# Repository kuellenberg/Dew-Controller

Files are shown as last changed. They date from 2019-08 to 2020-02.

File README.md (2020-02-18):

# Dew Controller

Microcontroller based project to control dew heater straps used on a telescope.

## Specification
* Operating voltage: 12V dc
* Power consumption (idle): t.b.d.
* 4 independently controlled heater channels
  * RCA jacks
  * Electronic overcurrent and short circuit protection
  * Total output current: 3.5 A max.
* 12 x 2 OLED display
* External temperature and humidity sensor connected via RS232 interface
  * Uses Silicon Labs Si7006 precision sensor
    * +/-1°C max.
    * +/-5% RH max.
* Auxiliary NTC temperature sensor input for testing and calibration
* User-friendly menu with rotary encoder input

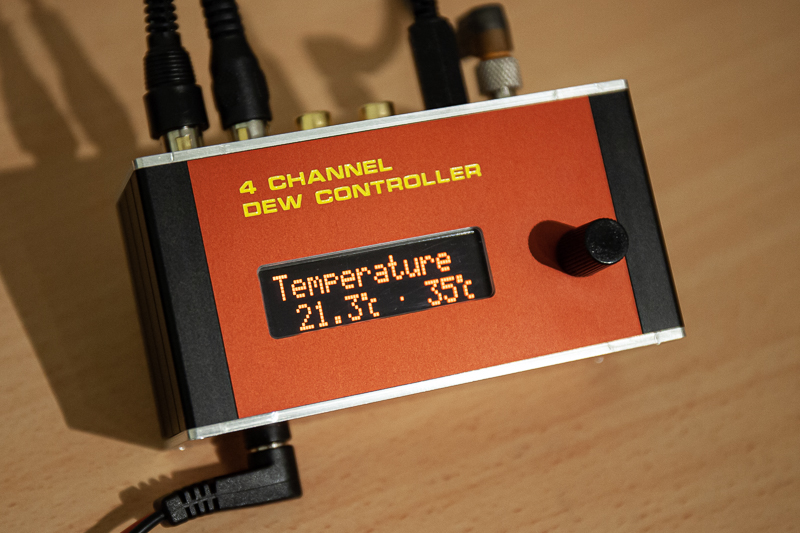
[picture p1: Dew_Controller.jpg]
Dew controller


## Theory of operation
The dew controller continuously calculates the required heating power for each connected dew heater strap based upon lens diameter and current temperature and humidity conditions. By carefully controlling the heating power negative seeing effects caused by undesired air movements are reduced to a minimum.
The underlying algorithm compensates for the rate of heat flow from the telescope lens to the cold sky, assuming that the telescope is equipped with a dew shield and only the circular area of the lens is exposed to the sky. An adjustable 'fudge factor' copes with all other deficiencies, like lack of thermal insulation from the heater straps. The theory gives very simular results to the rule of thumb given by [1].

## Hardware
### Controller Unit
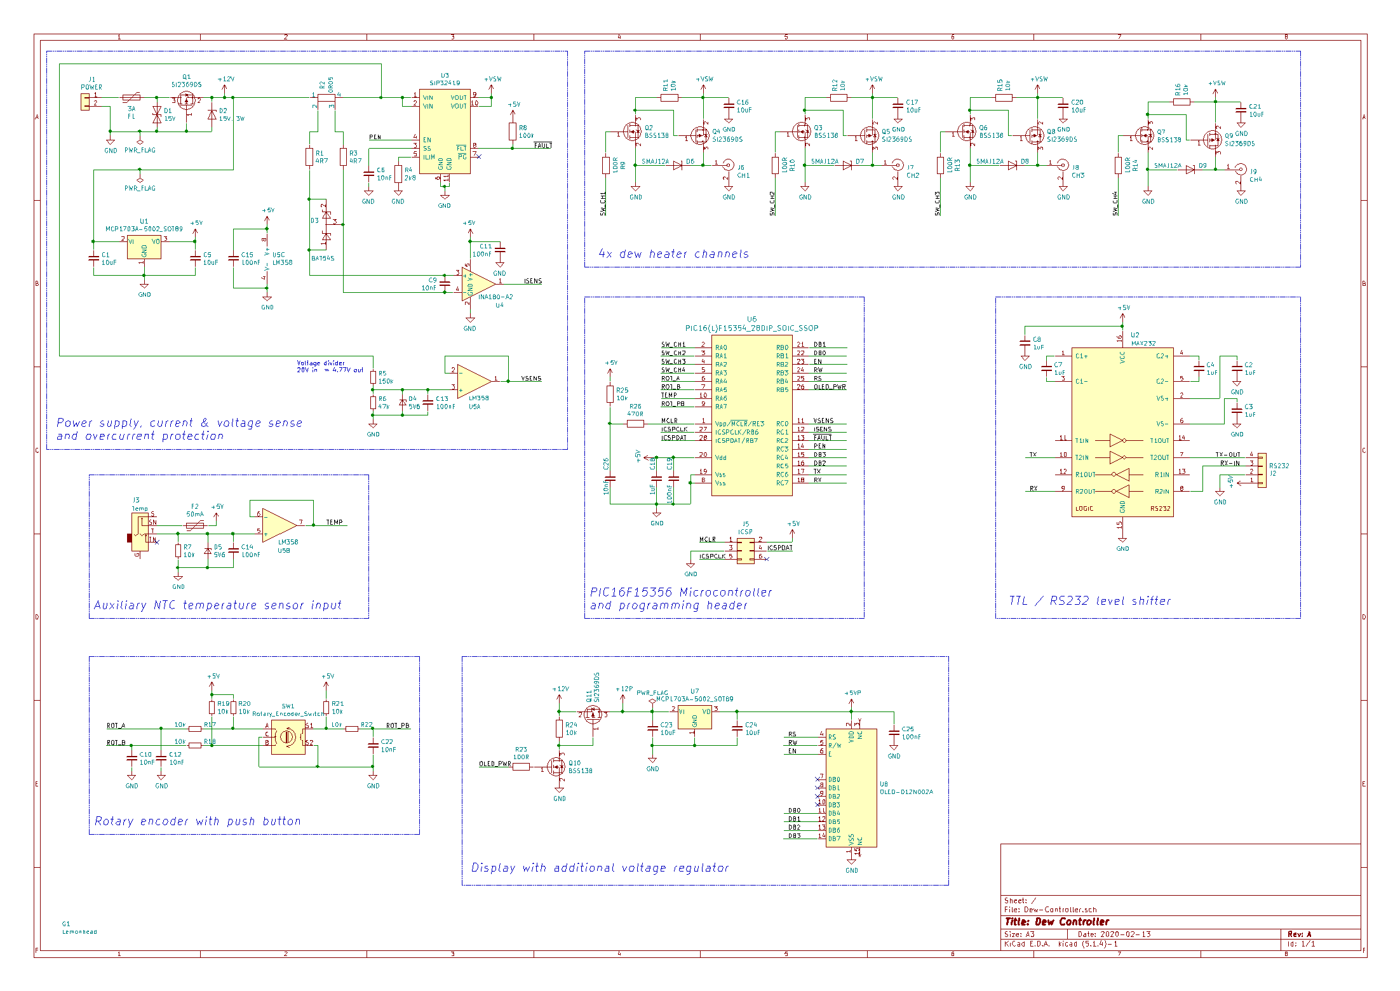
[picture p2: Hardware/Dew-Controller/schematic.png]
Schematic Dew Controller

The dew controller is build around a PIC16F15356 microcontroller with 16k words of flash memory and 2kB of RAM. It is configured to run at a clock frequency of 4.0 MHz, generated by its internal oscillator. With hindsight, regarding flash memory size and the string constants required by the menu system, the part wasn't the optimal choice. Without compiler optimizations the code doesn't fit on the device. For the next revision of the hardware a pin compatible PIC18F should be considered.

Since the controller has to be capable of measuring the current on each heater channel, the circuit comprises a TI INA180 high side current sense amplifier. To reduce cost and complexity, only a single amplifier is used and firmware measures the current of each channel sequentially. As for overcurrent and short circuit protection, an integrated solution is used. The Vishay SiP32419 is a load switch with programmable current limit up to 3.5A and eliminates the need for a conventional fuse (for which you'll never bring any spares, when you operate the device on a field trip).

The input voltage is measured with a simple voltage divider, buffered by 1/2 LM358. The other half of the Opamp is used for buffering the auxiliary NTC temperature sensor input.

It turned out that the switch mode regulator used on the OLED display module injects a lot of conducted noise back into the supply rails, which seriously impacts the performance of the microcontroller's ADC. The easiest way to block the noise from getting into the microcontroller was using a dedicated linear regulator for the display module. The regulator can be turned off via a MOSFET to save power during standby operation.

The device's menu system is entirely operated by a single rotary encoder with integrated push button. Although the quadrature signals are rudimentary low pass filtered, further debouncing is required in software.

High side P-channel MOSFETs are used to operate the four heater channels. 

The external temperature and humidity sensor is connected via an RS-232 interface, providing flexibility when testing different types of sensors. Although technically, the RS-232 level shifter isn't necessary if short cables are used, it gives good ESD protection and some extra noise immunity.

#### Case design
The housing is designed with [Schaeffer AG Frontplatten Designer](https://www.schaeffer-ag.de/frontplatten-designer)

### Sensor Box
The sensor circuit is very simple. It uses the PIC16F325 with 8k words flash memory and 1kB RAM. Unlike the controller circuit, it is powered by a 3.3V regulator. The Si7006 temperature and humidity sensor via connected I2C. RS-232 level shifting is done by a MAX3232. The PCB is designed to fit into a Hammond 1551 case with custom lid.

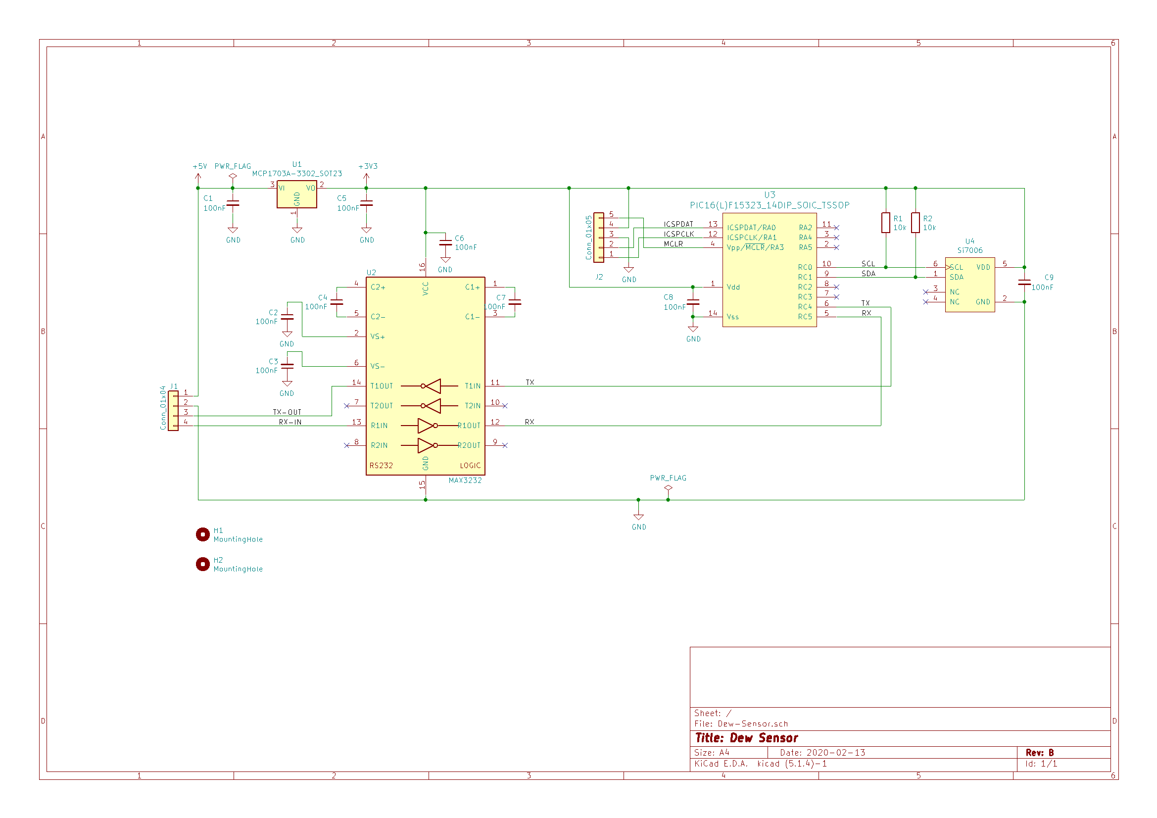
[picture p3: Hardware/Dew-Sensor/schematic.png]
Schematic Dew Sensor


## Firmware
Firmware development is done in MPLAB X with XC8 compiler. 

t.b.c.

___
[1]: G. D. Roth, Handbuch für Sternfreunde. Band 1: Technik und Theorie. ISBN 978-3-662-35367-7

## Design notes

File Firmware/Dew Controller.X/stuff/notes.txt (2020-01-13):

--- DATA STRUCTURE ---
--- GLOBAL ---
voltage
voltage min 
actual power 
temperature
humidity
dewpoint
temp_aux
dp offset
sky temp
fudge factor
groupA[4], groupB[4]

--- PER CHANNEL ---
current
max power Pmax
power required Preq
power attained Patt
duty cycle required DCreq
duty cycle attained DCatt
mode:auto|manual
status:on|off|open|short|disabled|removed
lens diameter

--- PERSISTENT DATA ---
chX
	lens dia
	mode (auto|manual)
	power

--- STATUS WORD ---
0 = ok, 1 = warning
Battery low
No sensor unit
No aux temp
typedef struct {
	unsigned BATLO:1;
	unsigned NOSENSOR:1;
	unsigned NOAUXTEMP:1;
} STATUS

--- ERROR MESSAGE ---
signed int8_t g_mp = -1;
function addMessage(message number)
	add message to message stack
	uint8_t messages[MESSAGE_STACK];
	if mp <= MESSAGE_STACK mp++;
	else f*ck it
	messages[mp] = message number;

function showMessages()
	static scrollPos;
	scroll through message[mp]
	if key mp-- & scrollPos = 0;

--- MAIN LOOP ---
read temp, humi, dp over rs232
	no data?
		if STATUS.NOSENSOR == 0 
			warning: check sensor 
		STATUS.NOSENSOR = 1;
		
read aux temp
	value out of range?
		STATUS.NOAUXTEMP = 1;
		
read voltage
read current
calc total power

current > [max load switch current] -> overcurrent (shouldn't happen)
	turn all channels off
	turn off load switch
		measure current again
		still overcurrent?
			show error!
	show error!

test voltage level
	voltage < [turn off]
		turn off load switch
		turn off oled
		power save 
	voltage min > [turn off] < [warn low]
		show warning low bat
	voltage > [warn high] < [crit]
		show warning high bat
	voltage > [crit]
		turn off oled power and load switch
		power save

calculate required power for each heater
	thermal radiation / stefan bolzman law
		epsilon = 0,95
		rho = 5,67e-8
		d = 0,0254 * lens dia
		A = PI * d^2 / 4
		T1 = tau + offset + 273,15
		T2 = tsky + 273,15
		phi = epsilon * rho * A * (T1^4 - T2^4)		
		
	Approx. heater temp. required
		p = 2 * PI * 0,0254 * lens dia
		b = 0,03 (width heat strip)
		A = p * b
		k = 0,85 (glas)
		Rth = lens dia/2 * (k * A)
		dt = phi * Rth - tau
	
	Preq = phi * fudge factor

control loop idle?
	test each heater
		if not disabled
			switch on 
			read voltage
			read current
			switch off
			store min. voltage
			current < xxx -> open
				if status changed?
					status = removed
					show warning heater removed
			current > xxx -> short
				fault detected? 
					status = disabled
					clear fault (cycle load switch)
					show warning heater short
			calculate Pmax
				Pmax = voltage * current
		
	calculate duty cycle for each channel
		DC = Pmax / Prequired
	
	optimize channel utilization
	start control loop
	
show warnings

show menu
	
--- INTERRUPT SERVICE ROUTINES ---
control loop (every 100ms)
	if not idle?
		counter < 1000?
			counter++;
		foreach channel in groupA
			counter <= DC?
				switch on
			else
				switch off
				channel in groupB?
					counter <= DC?
						switch on
					else 
						switch off
		idle = true

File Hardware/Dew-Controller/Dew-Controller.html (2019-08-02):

# BOM Rev

Date

Company

Comment 1

Comment 2

Comment 3

Comment 4

Total Parts

# 92 (Unique 43)

Ref

Qty

Value

Footprint

Datasheet

Manufacturer

Mouser

[C] -

C1 C5 C23 C24

4

10uF

Capacitor_SMD:C_1206_3216Metric

~

GRJ31CR71E106KE11L

81-GRJ31CR71E106KE1L

C2 C3 C4 C7 C8

5

1uF

Capacitor_SMD:C_0805_2012Metric

~

CC0805KKX7R9BB105

603-CC805KKX7R9BB105

C6 C9 C10 C12 C22 C26

6

10nF

Capacitor_SMD:C_0603_1608Metric

~

C0603Y103K5RACAUTO

80-C0603Y103K5RAUTO

C11 C13 C14 C15 C19

5

100nF

Capacitor_SMD:C_0603_1608Metric

~

C0603X104K5RAC7411

80-C0603X104K5R7411

C16 C17 C20 C21

4

10uF

Capacitor_SMD:C_1206_3216Metric

~

TCJA106M025R0150

581-TCJA106M025R0150

C18

1

1uF

Capacitor_SMD:C_0603_1608Metric

~

CGA3E1X7R1E105K080AE

810-CGA3E1X7R1E105KA

C25

1

100nF

Capacitor_SMD:C_0805_2012Metric

~

885012207098

710-885012207098

[D] -

D1

1

15V

Diode_SMD:D_SMB

~

SMBJ15CA-Q

652-SMBJ15CA-Q

D2

1

15V, 3W

Diode_SMD:D_SMB

~

1SMB5929BT3G

863-1SMB5929BT3G

D3

1

BAT54S

Package_TO_SOT_SMD:SOT-23

https://www.diodes.com/assets/Datasheets/ds11005.pdf

BAT54S-7-F

621-BAT54S-F

D4 D5

2

5V6

Diode_SMD:D_SOD-523

~

MM5Z5V6T1G

863-MM5Z5V6T1G

D6 D7 D8 D9

4

SMAJ12A

Diode_SMD:D_SMA

~

SMAJ12A

576-SMAJ12A

[F] -

F1

1

3A

ak:Fuse_2920_7451Metric

~

0ZCF0300BF2C

530-0ZCF0300BF2C

F2

1

50mA

ak:Fuse_0603_1608Metric

~

MH2029-601Y

652-MH2029-601Y

[G] -

G1

1

Lemonhead

ak:lemonhead

[J] -

J1

1

POWER

Connector_JST:JST_XH_B02B-XH-A_1x02_P2.50mm_Vertical

~

J2

1

RS232

Connector_JST:JST_XH_B04B-XH-A_1x04_P2.50mm_Vertical

~

J3

1

Temp

ak:MJ-2509N

~

MJ-2509N

490-MJ-2509N

J5

1

ICSP

ak:MicroMatch-Female-6P

~

215079-6

571-215079-6

J6

1

CH1

ak:PJRAN1X1U

~

PJRAN1X1U03AUX

502-PJRAN1X1U03AUX

J7

1

CH2

ak:PJRAN1X1U

~

PJRAN1X1U03AUX

502-PJRAN1X1U03AUX

J8

1

CH3

ak:PJRAN1X1U

~

PJRAN1X1U03AUX

502-PJRAN1X1U03AUX

J9

1

CH4

ak:PJRAN1X1U

~

PJRAN1X1U03AUX

502-PJRAN1X1U03AUX

[Q] -

Q1 Q4 Q5 Q8 Q9 Q11

6

SI2369DS

Package_TO_SOT_SMD:SOT-23

~

SI2369DS-T1-GE3

78-SI2369DS-T1-GE3

Q2 Q3 Q6 Q7 Q10

5

BSS138

Package_TO_SOT_SMD:SOT-23

~

BSS138P 215

771-BSS138P215

[R] -

R1 R3

2

4R7

Resistor_SMD:R_0603_1608Metric

~

ESR03EZPJ4R7

755-ESR03EZPJ4R7

R2

1

0R05

ak:R_Shunt_Ohmite_LVK12

~

LVK12R050DER

588-LVK12R050DER

R4

1

2k8

Resistor_SMD:R_0603_1608Metric

~

AC0603FR-072K8L

603-AC0603FR-072K8L

R5

1

150k

Resistor_SMD:R_0603_1608Metric

~

RC0603FR-07150KL

603-RC0603FR-07150KL

R6

1

47k

Resistor_SMD:R_0603_1608Metric

~

SFR03EZPF4702

755-SFR03EZPF4702

R7 R17 R18 R19 R20 R21 R22 R25

8

10k

Resistor_SMD:R_0603_1608Metric

~

RC0603FR-0710KL

603-RC0603FR-0710KL

R8

1

100k

Resistor_SMD:R_0603_1608Metric

~

SFR03EZPF1003

755-SFR03EZPF1003

R9 R10 R13 R14 R23

5

100R

Resistor_SMD:R_0805_2012Metric

~

CRGP0805F100R

279-CRGP0805F100R

R11 R12 R15 R16 R24

5

10k

Resistor_SMD:R_0805_2012Metric

~

ERJ-6ENF1002V

667-ERJ-6ENF1002V

R26

1

470R

Resistor_SMD:R_0603_1608Metric

~

RC0603FR-07470RL

603-RC0603FR-07470RL

[SW] -

SW1

1

Rotary_Encoder_Switch

ak:RotaryEncoder_Alps_EC11E-Switch_Vertical_H20mm

~

EC11E183440C

688-EC11E183440C

[U] -

U1 U7

2

MCP1703A-5002_SOT89

Package_TO_SOT_SMD:SOT-89-3

http://ww1.microchip.com/downloads/en/DeviceDoc/20005122B.pdf

PIC16F15354-I/SO

579-MCP1703AT5002EMB

U2

1

MAX232

ak:SOIC-16W_5.3x10.2mm_P1.27mm

http://www.ti.com/lit/ds/symlink/max232.pdf

MAX232NSR

595-MAX232NSR

U3

1

SIP32419

ak:DFN-10-1EP_3x3mm_P0.5mm_EP1.4x2.3mm

SIP32419DN-T1-GE4

78-SIP32419DN-T1-GE4

U4

1

INA180-A2

Package_TO_SOT_SMD:SOT-23-5

http://www.ti.com/lit/ds/symlink/ina181.pdf

INA180A2IDBVR

595-INA180A2IDBVR

U5

1

LM358

Package_SO:VSSOP-8_3.0x3.0mm_P0.65mm

http://www.ti.com/lit/ds/symlink/lm2904-n.pdf

LM358LVIDGKR

595-LM358LVIDGKR

U6

1

PIC16(L)F15354_28DIP_SOIC_SSOP

Package_SO:SOIC-28W_7.5x17.9mm_P1.27mm

PIC16F15354-I/SO

579-PIC16F15354-I/SO

U8

1

OLED-012N002A

ak:OLED012N002A

http://www.newhavendisplay.com/specs/NHD-0420H1Z-FSW-GBW-33V3.pdf

O012N002ARPP5N0000

78-012N002ARPP5N0000

# BOM made with KICAD_BOM_WIZARD (https://github.com/HashDefineElectronics/KiCad_BOM_Wizard) (Generated Wed 13 Mar 2019 05:19:53 PM CET)

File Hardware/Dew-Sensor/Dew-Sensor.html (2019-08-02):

# BOM Rev

Date

Company

Comment 1

Comment 2

Comment 3

Comment 4

Total Parts

# 20 (Unique 10)

Ref

Qty

Value

Footprint

Datasheet

Manufacturer

Mouser

[C] -

C1 C2 C3 C4 C5 C6 C7 C8 C9

9

100nF

Capacitor_SMD:C_0805_2012Metric

~

885012207098

710-885012207098

[G] -

G1

1

Lemonhead

ak:lemonhead

[H] -

H1 H2

2

MountingHole_Pad

MountingHole:MountingHole_2.5mm_Pad

~

[J] -

J1

1

Conn_01x04

Connector_PinSocket_2.54mm:PinSocket_1x04_P2.54mm_Horizontal

~

TSW-104-08-L-S-RA

200-TSW10408LSRA

J2

1

Conn_01x05

Connector_PinSocket_1.27mm:PinSocket_1x05_P1.27mm_Vertical

~

M50-3030542

855-M50-3030542

[R] -

R1 R2

2

10k

Resistor_SMD:R_0805_2012Metric

~

ERJ-6ENF1002V

667-ERJ-6ENF1002V

[U] -

U1

1

MCP1703A-3302_SOT23

Package_TO_SOT_SMD:SOT-23

http://ww1.microchip.com/downloads/en/DeviceDoc/20005122B.pdf

MCP1703AT-3302E/CB

579-MCP1703AT3302ECB

U2

1

MAX3232

Package_SO:SOIC-16_3.9x9.9mm_P1.27mm

https://datasheets.maximintegrated.com/en/ds/MAX3222-MAX3241.pdf

MAX3232IDR

595-MAX3232IDR

U3

1

PIC16(L)F15323_14DIP_SOIC_TSSOP

Package_SO:SOIC-14_3.9x8.7mm_P1.27mm

PIC16F15323-I/SL

579-PIC16F15323-I/SL

U4

1

Si7006

ak:SI7006-A20

SI7006-A20-IM1R

634-SI7006-A20-IM1R

# BOM made with KICAD_BOM_WIZARD (https://github.com/HashDefineElectronics/KiCad_BOM_Wizard) (Generated Wed 20 Mar 2019 07:00:30 PM CET)

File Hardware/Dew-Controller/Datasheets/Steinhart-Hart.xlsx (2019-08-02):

R0 | 10000 |  |  | 1.97
B | 3380 |  |  | 1.68
T0 | 298.15 |  |  | 0.66
r | 0.1192855385
Rs | 33000 |  |  | 610.2996911
U | 3.3 |  |  | 9.25337405 | 0.09831235519
Iconst | 2e-05
T | R | I | U0 | U1 | U2 | ADC1 | ADC2
-30 | 129916.7384 | 2.025574555e-05 | 2.60 | 2.63 | 3.30 | 815.783723 | 1023
-20 | 75021.6899 | 3.054942024e-05 | 1.50 | 2.29 | 2.73 | 710.4794309 | 846.486244
-10 | 45168.27118 | 4.221661743e-05 | 0.90 | 1.91 | 2.09 | 591.1240036 | 646.4196146
0 | 28223.72509 | 5.390067323e-05 | 0.56 | 1.52 | 1.44 | 471.5961128 | 446.0638974
10 | 18231.39918 | 6.441362236e-05 | 0.36 | 1.17 | 0.86 | 364.0486433 | 265.7900697
20 | 12133.17001 | 7.311695588e-05 | 0.24 | 0.89 | 0.38 | 275.0135414 | 116.5471476
30 | 8294.606244 | 7.991358437e-05 | 0.17 | 0.66 | 0.00 | 205.4840319 | 0

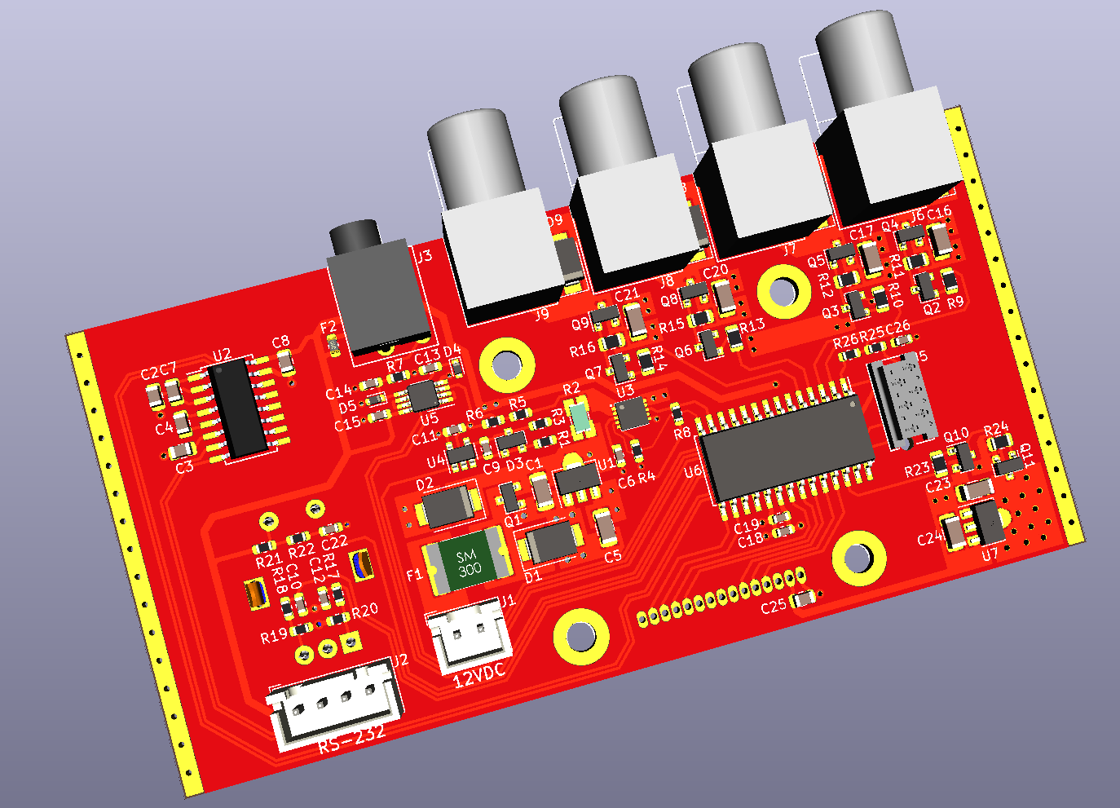
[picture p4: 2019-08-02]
Hardware/Dew-Controller/PCB.png

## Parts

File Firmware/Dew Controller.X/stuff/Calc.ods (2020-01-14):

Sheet: Tabelle1
U1 | 12
R1 | 150
R2 | 47
U2 | 2,862944162
N | 1023
Uref | 5
counts | 610
U2(counts) | 12,49662029
 | 1249280
Rsh | 0,05
A | 50
N | 1023
Uref | 5
Counts | 1
I | 0,001955034 | 195,5034213

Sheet: timer0
Fosc | 4,00E+006 | Hz
Fosc/4 | 1000000 | Hz
Presc | 128
 | 7812,5 | Hz
Postsc | 1
 | 7812,5 | Hz
Bits | 256
Tmax | 0,032768 | s
Required | 0,01 | s
TMR0 | 177,875
Actual | 0,010112 | s

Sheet: timer1
Fosc | 4,00E+006 | Hz
Fosc/4 | 1000000 | Hz
Presc | 8
 | 125000 | Hz
Bits | 65535
Tmax | 0,52428 | s
Required | 0,1 | s
TMR1 | 53035
Actual | 0,1 | s

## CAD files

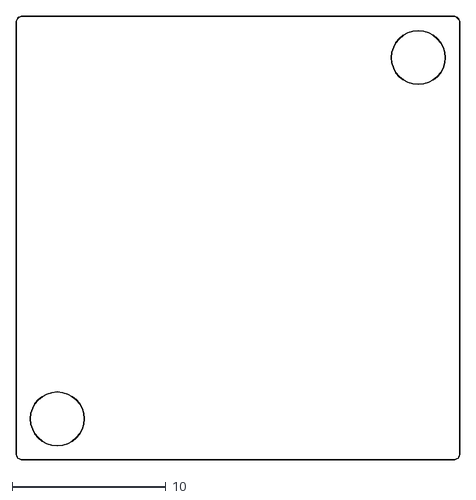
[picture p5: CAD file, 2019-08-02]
Hardware/Lid/Datasheets/outline.dxf
28.9 x 28.9

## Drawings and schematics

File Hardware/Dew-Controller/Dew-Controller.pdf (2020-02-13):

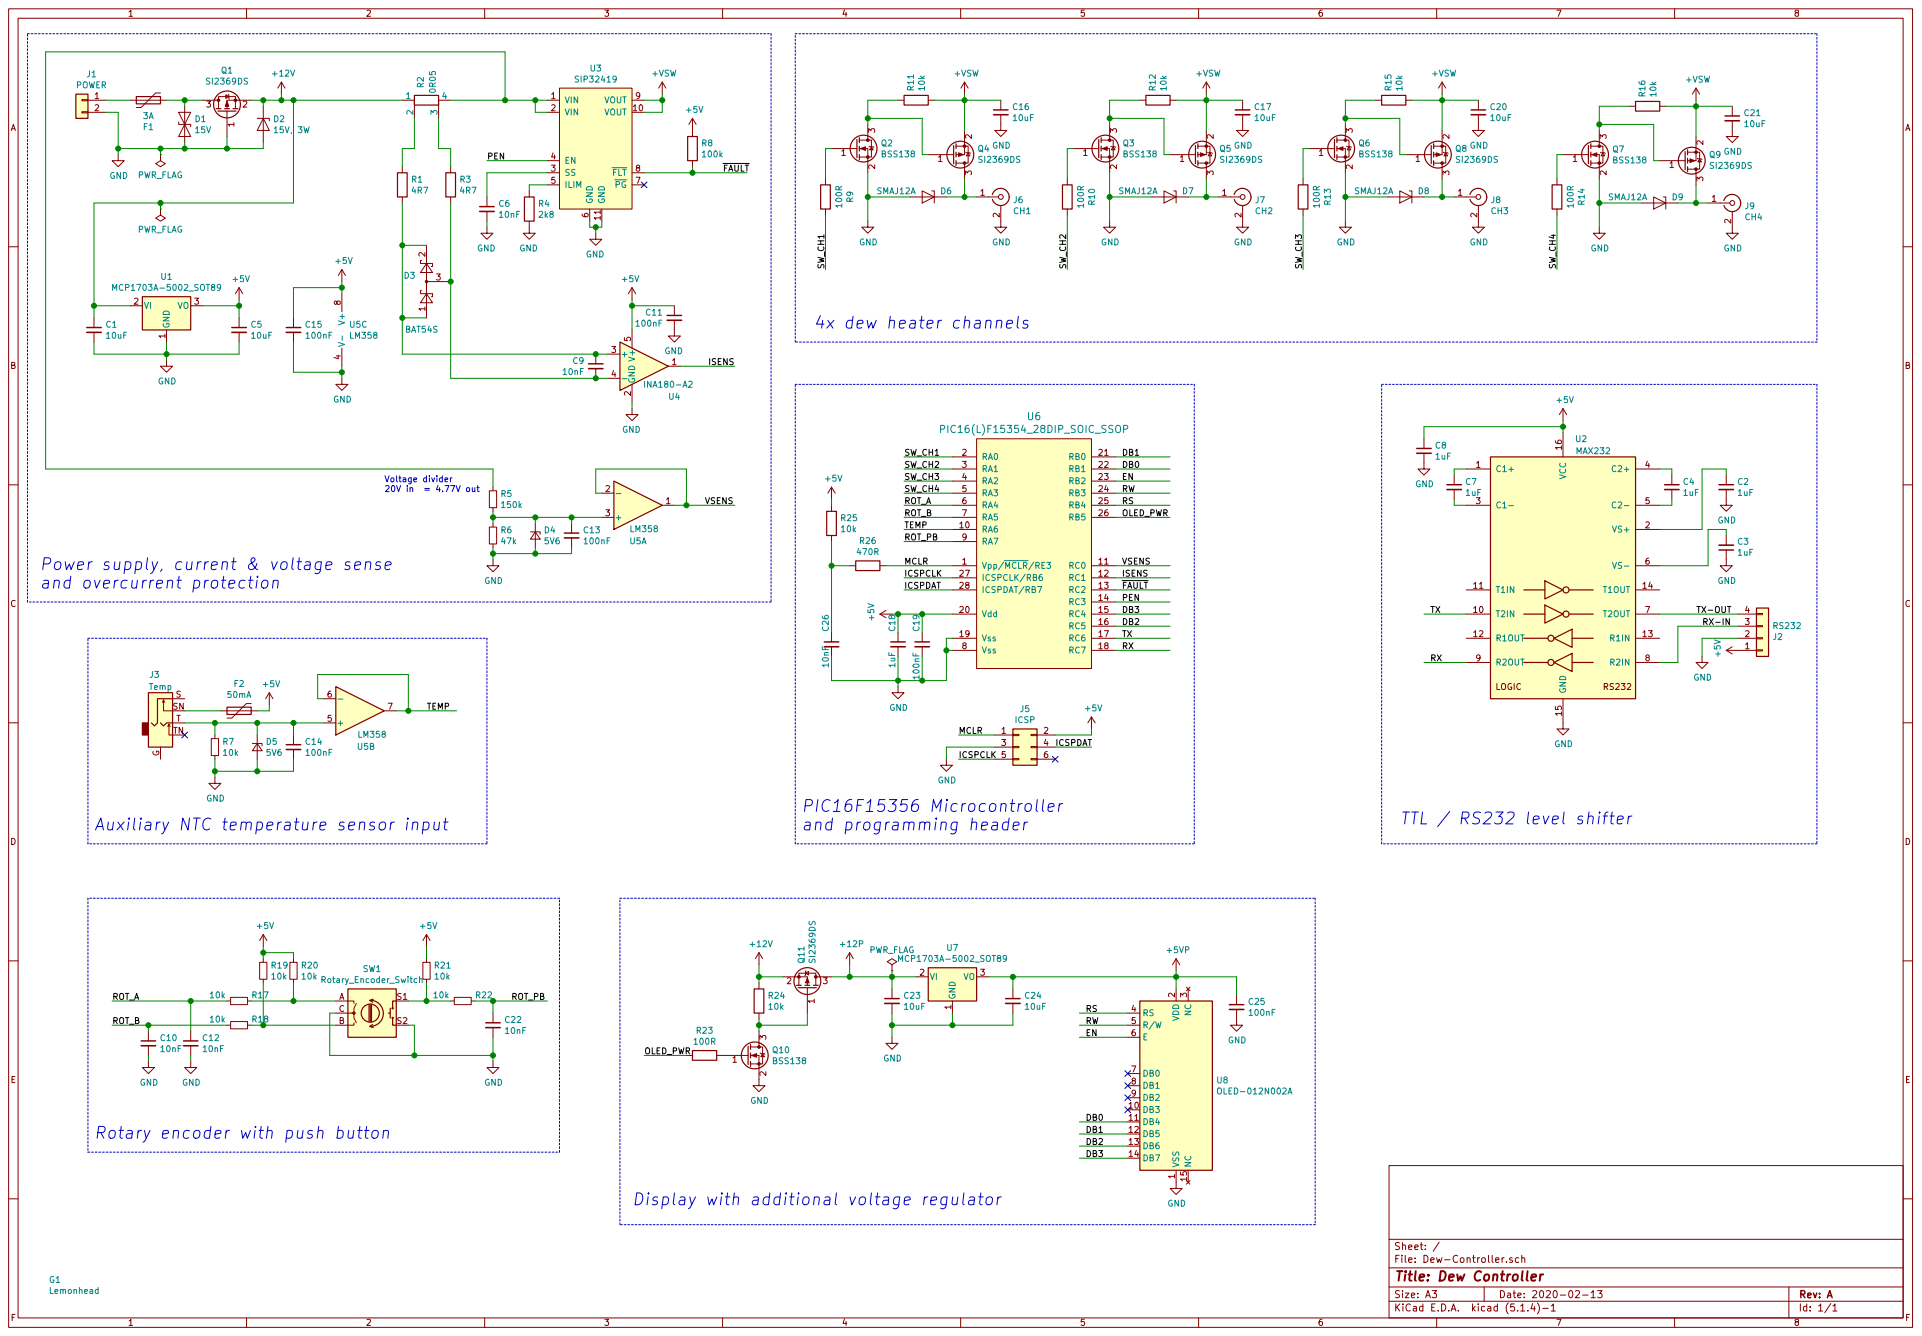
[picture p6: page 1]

Voltage divider 20V in = 4.77V out

Power supply, current & voltage sense
and overcurrent protection

RS Rotary encoder with push button

Display with additional voltage regulator

Id: 1/1 Title: Dew Controller File: Dew-Controller.sch Sheet: /

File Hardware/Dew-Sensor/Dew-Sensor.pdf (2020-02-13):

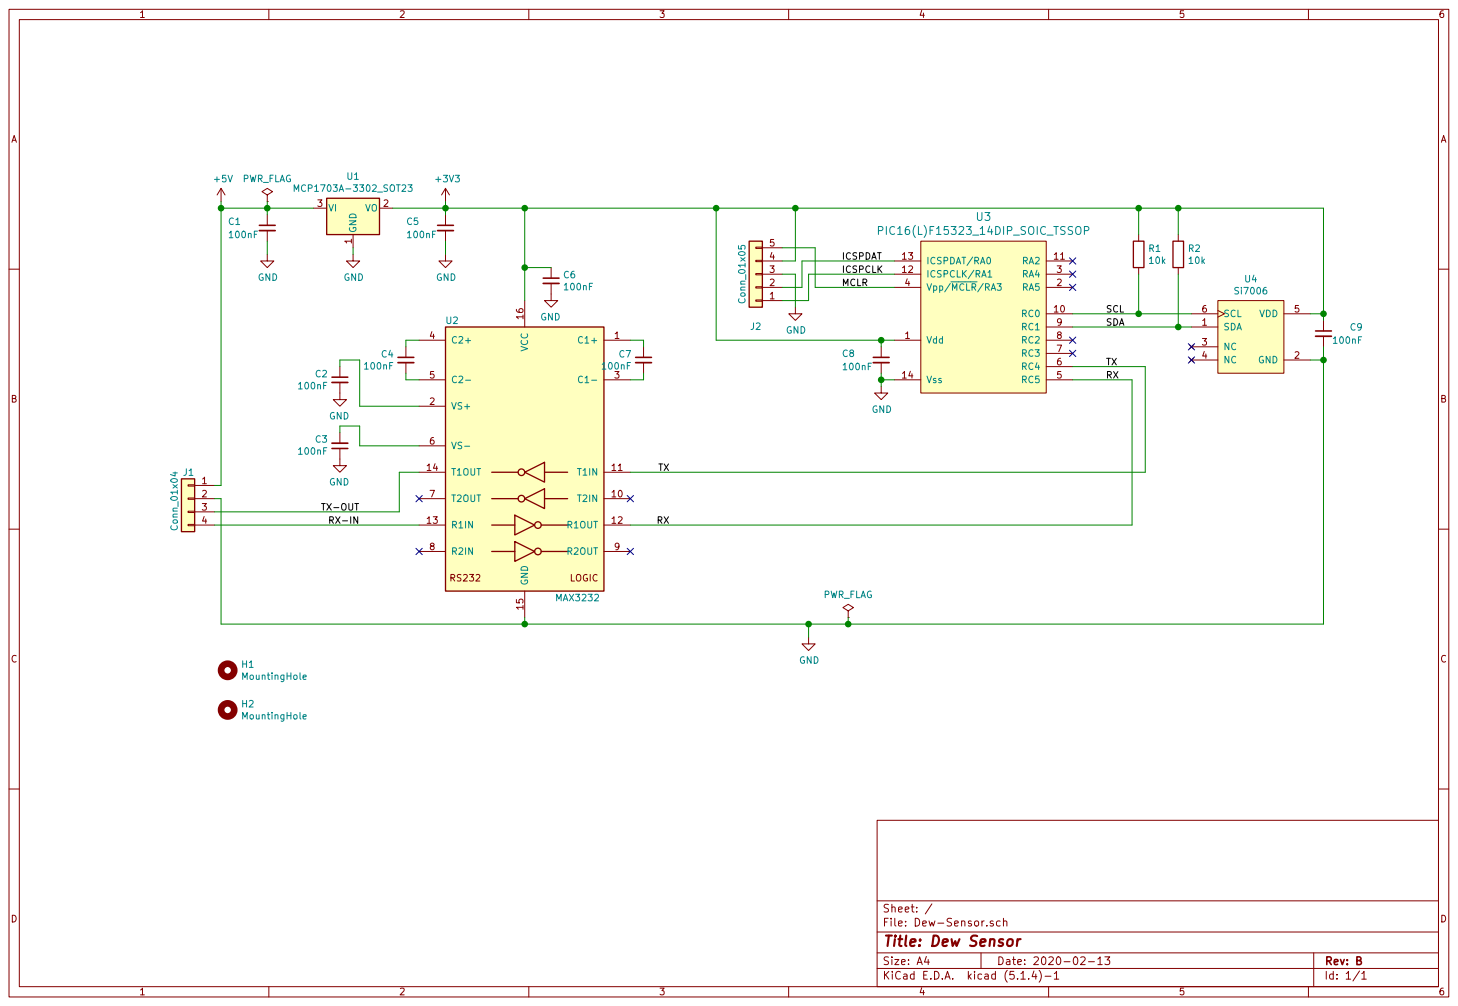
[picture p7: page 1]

3 | ICSPCLK MCLR | ICSPCLK/RA1 12

Id: 1/1 Title: Dew Sensor File: Dew-Sensor.sch Sheet: / PWR_FLAG

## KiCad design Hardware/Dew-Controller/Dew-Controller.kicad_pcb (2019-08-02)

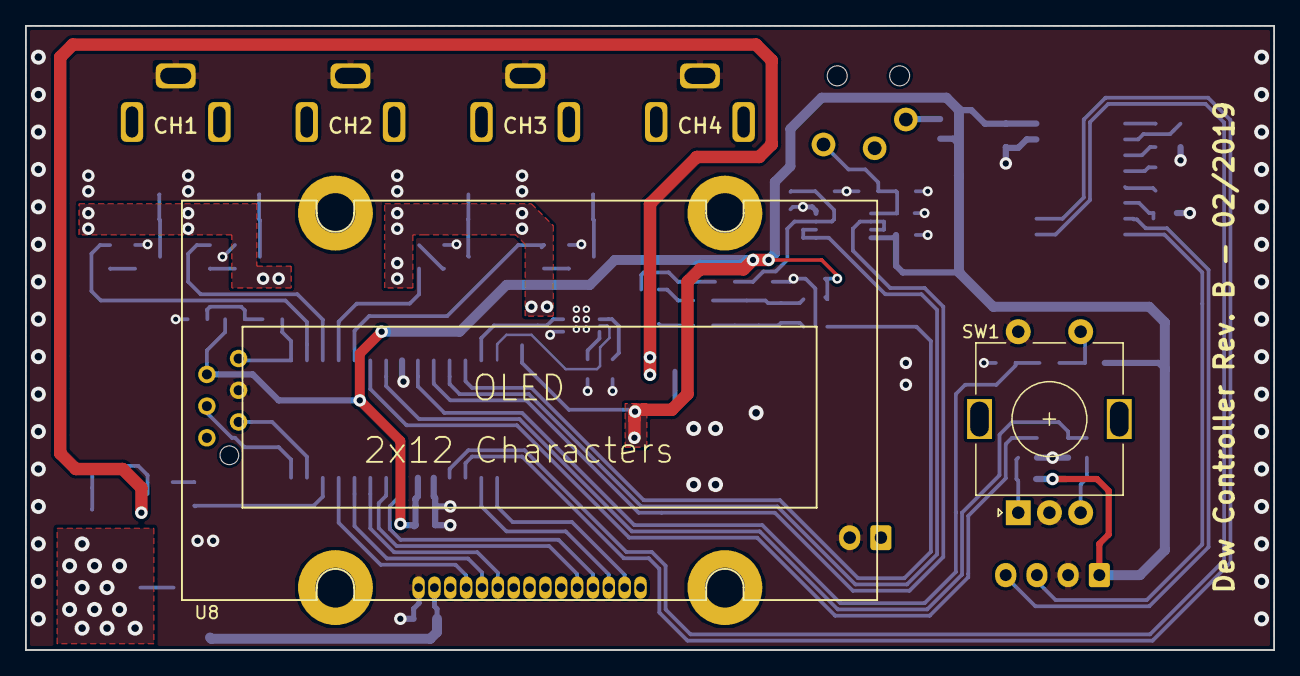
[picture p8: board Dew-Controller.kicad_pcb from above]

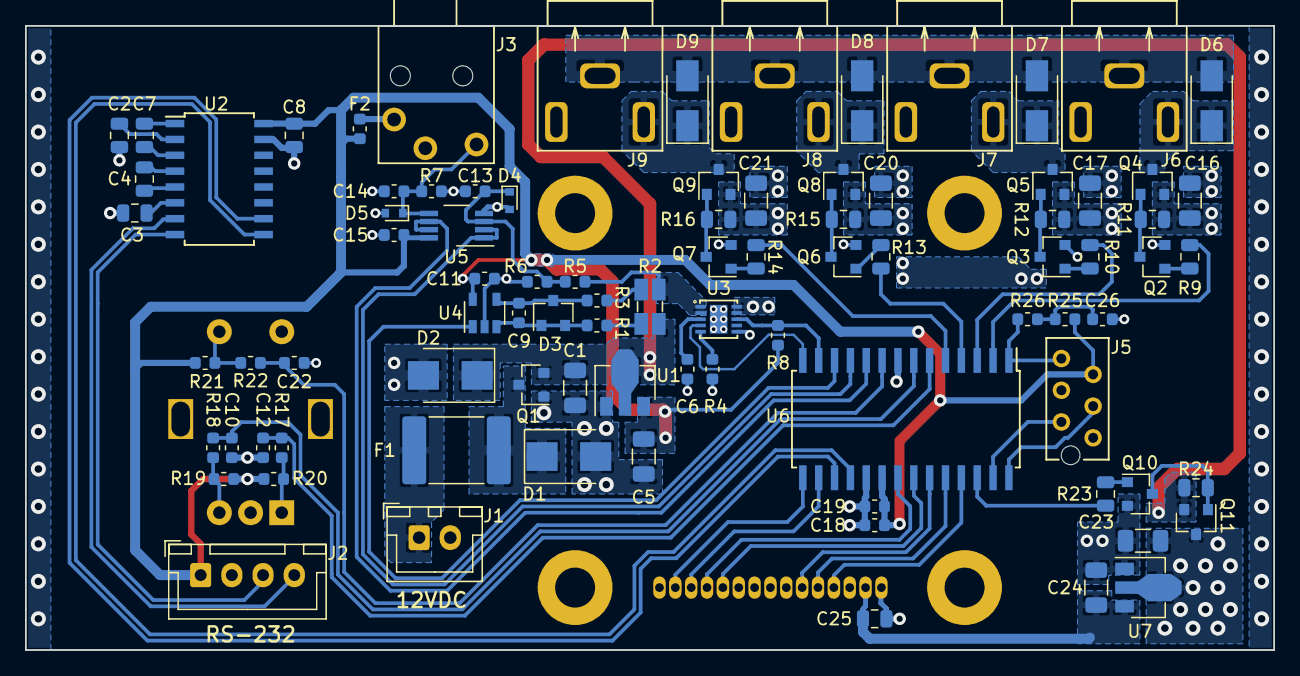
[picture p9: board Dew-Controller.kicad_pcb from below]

Board: 2 copper layers, 100.0 x 50.0 mm, 92 parts (89 on the bottom side), 69 nets.

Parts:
C1, C5, C16, C17, C20, C21, C23, C24: 10uF; C_1206_3216Metric
C2, C3, C4, C7, C8: 1uF; C_0805_2012Metric
C6, C9, C10, C12, C22, C26: 10nF; C_0603_1608Metric
C11, C13, C14, C15, C19: 100nF; C_0603_1608Metric
C18: 1uF; C_0603_1608Metric
C25: 100nF; C_0805_2012Metric
D1: 15V; D_SMB
D2: 15V, 3W; D_SMB
D3: BAT54S; SOT-23
D4, D5: 5V6; D_SOD-523
D6, D7, D8, D9: SMAJ12A; D_SMA
F1: 3A; Fuse_2920_7451Metric
F2: 50mA; Fuse_0603_1608Metric
G1: Lemonhead; lemonhead
J1: POWER; JST_XH_B02B-XH-A_1x02_P2.50mm_Vertical
J2: RS232; JST_XH_B04B-XH-A_1x04_P2.50mm_Vertical
J3: Temp; MJ-2509N
J5: ICSP; MicroMatch-Female-6P
J6: CH1; PJRAN1X1U
J7: CH2; PJRAN1X1U
J8: CH3; PJRAN1X1U
J9: CH4; PJRAN1X1U
Q1, Q4, Q5, Q8, Q9, Q11: SI2369DS; SOT-23
Q2, Q3, Q6, Q7, Q10: BSS138; SOT-23
R1, R3: 4R7; R_0603_1608Metric
R2: 0R05; R_Shunt_Ohmite_LVK12
R4: 2k8; R_0603_1608Metric
R5: 150k; R_0603_1608Metric
R6: 47k; R_0603_1608Metric
R7, R17, R18, R19, R20, R21, R22, R25: 10k; R_0603_1608Metric
R8: 100k; R_0603_1608Metric
R9, R10, R13, R14, R23: 100R; R_0805_2012Metric
R11, R12, R15, R16, R24: 10k; R_0805_2012Metric
R26: 470R; R_0603_1608Metric
SW1: Rotary_Encoder_Switch; RotaryEncoder_Alps_EC11E-Switch_Vertical_H20mm
U1, U7: MCP1703A-5002_SOT89; SOT-89-3
U2: MAX232; SOIC-16W_5.3x10.2mm_P1.27mm
U3: SIP32419; DFN-10-1EP_3x3mm_P0.5mm_EP1.4x2.3mm
U4: INA180-A2; SOT-23-5
U5: LM358; VSSOP-8_3.0x3.0mm_P0.65mm
U6: PIC16(L)F15354_28DIP_SOIC_SSOP; SOIC-28W_7.5x17.9mm_P1.27mm
U8: OLED-012N002A; OLED012N002A

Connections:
+5V: C5.1, C8.1, C11.1, C15.1, C18.1, C19.1, F2.1, J2.1, J5.2, R8.1, R19.1, R20.1, R21.1, R25.1, U1.3, U2.16, U4.5, U5.8, U6.20
+5VP: C24.1, C25.1, U7.3, U8.2
+12P: C23.1, Q11.3, U7.2
+12V: C1.1, D2.1, Q1.2, Q11.2, R2.1, R24.1, U1.2
+VSW: C16.1, C17.1, C20.1, C21.1, Q4.2, Q5.2, Q8.2, Q9.2, R11.2, R12.2, R15.2, R16.2, U3.9, U3.10
/DB0: U6.22, U8.11
/DB1: U6.21, U8.12
/DB2: U6.16, U8.13
/DB3: U6.15, U8.14
/EN: U6.23, U8.6
/ICSPCLK: J5.5, U6.27
/ICSPDAT: J5.4, U6.28
/ISENS: U4.1, U6.12
/MCLR: J5.1, R26.1, U6.1
/OLED_PWR: R23.2, U6.26
/PEN: U3.4, U6.14
/ROT_A: C12.1, R17.2, U6.6
/ROT_B: C10.1, R18.2, U6.7
/ROT_PB: C22.1, R22.1, U6.9
/RS: U6.25, U8.4
/RW: U6.24, U8.5
/RX: U2.9, U6.18
/RX-IN: J2.3, U2.8
/SW_CH1: R9.2, U6.2
/SW_CH2: R10.2, U6.3
/SW_CH3: R13.2, U6.4
/SW_CH4: R14.2, U6.5
/TEMP: U5.6, U5.7, U6.10
/TX: U2.10, U6.17
/TX-OUT: J2.4, U2.7
/VSENS: U5.1, U5.2, U6.11
/~FAULT: R8.2, U3.8, U6.13
GND: C1.2, C2.2, C3.1, C5.2, C6.2, C8.2, C10.2, C11.2, C12.2, C13.2, C14.2, C15.2, C16.2, C17.2, C18.2, C19.2, C20.2, C21.2, C22.2, C23.2, C24.2, C25.2, C26.2, D1.2, D2.2, D4.2, D5.2, D6.2, D7.2, D8.2, D9.2, J1.2, J2.2, J5.3, J6.2, J7.2, J8.2, J9.2, Q1.1, Q2.2, Q3.2, Q6.2, Q7.2, Q10.2, R4.2, R6.2, R7.2, SW1.C, SW1.S2, U1.1, U2.15, U3.6, U3.11, U4.2, U5.4, U6.8, U6.19, U7.1, U8.1
unnamed: C2.1, U2.2
unnamed: C3.2, U2.6
unnamed: C4.1, U2.4
unnamed: C4.2, U2.5
unnamed: C6.1, U3.3
unnamed: C7.1, U2.1
unnamed: C7.2, U2.3
unnamed: C9.1, D3.1, D3.2, R1.2, U4.3
unnamed: C9.2, D3.3, R3.2, U4.4
unnamed: C13.1, D4.1, R5.2, R6.1, U5.3
unnamed: C14.1, D5.1, J3.T, R7.1, U5.5
unnamed: C26.1, R25.2, R26.2
unnamed: D1.1, F1.2, Q1.3
unnamed: D6.1, J6.1, Q4.3
unnamed: D7.1, J7.1, Q5.3
unnamed: D8.1, J8.1, Q8.3
unnamed: D9.1, J9.1, Q9.3
unnamed: F1.1, J1.1
unnamed: F2.2, J3.S
unnamed: Q2.1, R9.1
unnamed: Q2.3, Q4.1, R11.1
unnamed: Q3.1, R10.1
unnamed: Q3.3, Q5.1, R12.1
unnamed: Q6.1, R13.1
unnamed: Q6.3, Q8.1, R15.1
unnamed: Q7.1, R14.1
unnamed: Q7.3, Q9.1, R16.1
unnamed: Q10.1, R23.1
unnamed: Q10.3, Q11.1, R24.2
unnamed: R1.1, R2.2
unnamed: R2.3, R3.1
unnamed: R2.4, R5.1, U3.1, U3.2
unnamed: R4.1, U3.5
unnamed: R17.1, R20.2, SW1.A
unnamed: R18.1, R19.2, SW1.B
unnamed: R21.2, R22.2, SW1.S1

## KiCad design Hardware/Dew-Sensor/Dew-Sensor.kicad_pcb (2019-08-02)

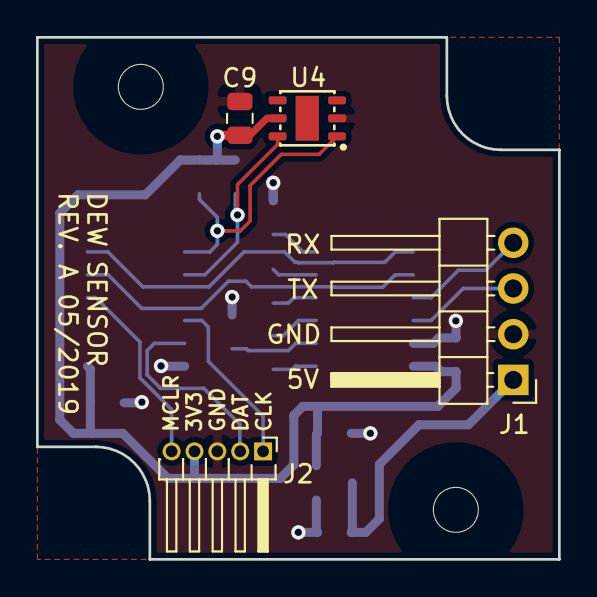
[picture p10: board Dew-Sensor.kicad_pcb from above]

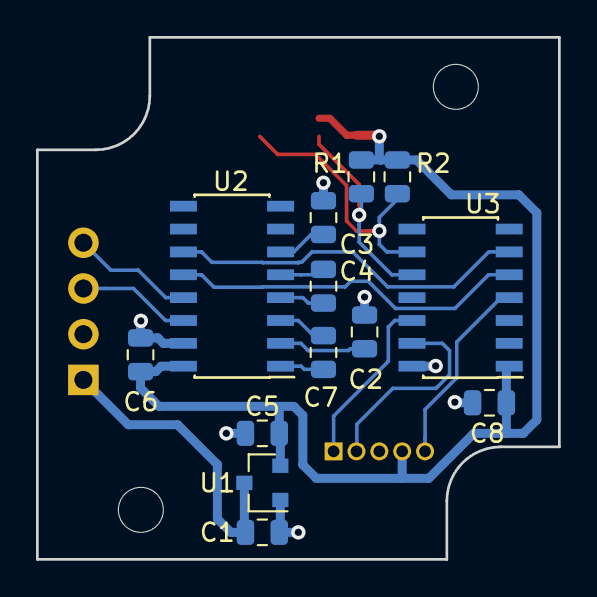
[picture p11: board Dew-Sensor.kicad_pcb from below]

Board: 2 copper layers, 29.0 x 29.0 mm, 19 parts (13 on the bottom side), 18 nets.

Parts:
C1, C2, C3, C4, C5, C6, C7, C8, C9: 100nF; C_0805_2012Metric
H1, H2: MountingHole; MountingHole_2.5mm
J1: Conn_01x04; PinHeader_1x04_P2.54mm_Horizontal
J2: Conn_01x05; PinHeader_1x05_P1.27mm_Horizontal
R1, R2: 10k; R_0805_2012Metric
U1: MCP1703A-3302_SOT23; SOT-23
U2: MAX3232; SOIC-16_3.9x9.9mm_P1.27mm
U3: PIC16(L)F15323_14DIP_SOIC_TSSOP; SOIC-14_3.9x8.7mm_P1.27mm
U4: Si7006; SI7006-A20

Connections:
+3V3: C5.1, C6.1, C8.1, C9.1, J2.4, R1.1, R2.1, U1.2, U2.16, U3.1, U4.5
+5V: C1.1, J1.1, U1.3
/ICSPCLK: J2.1, U3.12
/ICSPDAT: J2.2, U3.13
/MCLR: J2.5, U3.4
/RX: U2.12, U3.5
/RX-IN: J1.4, U2.13
/SCL: R1.2, U3.10, U4.6
/SDA: R2.2, U3.9, U4.1
/TX: U2.11, U3.6
/TX-OUT: J1.3, U2.14
GND: C1.2, C2.2, C3.1, C5.2, C6.2, C8.2, C9.2, J1.2, J2.3, U1.1, U2.15, U3.14, U4.2
unnamed: C2.1, U2.2
unnamed: C3.2, U2.6
unnamed: C4.1, U2.4
unnamed: C4.2, U2.5
unnamed: C7.1, U2.1
unnamed: C7.2, U2.3

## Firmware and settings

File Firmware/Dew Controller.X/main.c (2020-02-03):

/*
 * File:   main.c
 * Author: Andre
 *
 * Created on 12. Januar 2020, 13:20
 */
#include "common.h"
#include "io.h"
#include "config.h"
#include "menuhelper.h"
#include "system.h"
#include "memory.h"
#include "oled.h"
#include "interrupt.h"
#include "error.h"
#include "interrupt.h"
#include "inputs.h"

//-----------------------------------------------------------------------------
// Function Prototypes
//-----------------------------------------------------------------------------
void initialize(void);
void initGlobalData(void);

//-----------------------------------------------------------------------------
// Main program loop
//-----------------------------------------------------------------------------

void main(void)
{
	uint32_t sysCheckInterval = 0;
	uint8_t controllerIdle = 1;
	uint8_t initDone = 0;
	uint8_t displayOff = 0;

	initialize();
	OLED_PWR = 1;
	OLED_init();
	OLED_loadSpecialChars();
	OLED_command(OLED_RETURNHOME);
	OLED_command(OLED_CLEARDISPLAY);
	initGlobalData();
	PEN = 1;
	
	// Skip reading configuration from flash by pressing button during power up
	if (ROT_PB)
		readNVM();
	
	while (1) {
		// clear watchdog timer TODO: setup watchdog timer properly
		CLRWDT();

		// get battery voltage, current and aux. temperature
		getAnalogValues();
		// system check every 0.5s
		if (timeSince(sysCheckInterval) > 5) {
			sysCheckInterval = timeNow();
			systemCheck();
		}

		// query sensor
		if (checkSensor()) {
			// once new sensor data is ready, calculate required heater power
			calcRequiredPower();
			initDone = 1;
			//if ((data.status.SENSOR_OK) && (data.tempC < 1))
			//	NOP();
		}


		// is control loop running?
		if (controllerIdle) {
			if (initDone) {
				// Wait until initial sensor check is finished		
				// TODO: interval ?				
				checkChannelStatus();
				channelThing();
				controllerIdle = 0;
			}
		} else {
			// controller returns true after each cycle
			controllerIdle = controller();
		}
		
		if (getLastError() != NO_ERROR) {
			userActivity = timeNow();
			viewErrorMessage(); // Display last error message	
		} else if (! displayOff) {
			menu();
		}	
			
		// turn off display after DISPLAY_TIMEOUT
		if (displayOff && ((timeSince(userActivity) < DISPLAY_TIMEOUT))) {
			// wake up
			displayOff = 0;
			OLED_command(OLED_DISPLAYCONTROL | OLED_DISPLAYON);
		} else if (timeSince(userActivity) > DISPLAY_TIMEOUT) {
			displayOff = 1;
			OLED_command(OLED_DISPLAYCONTROL | OLED_DISPLAYOFF);
		} 		
		
		
		
		// Time to relax :-)
		__delay_ms(40);
		NOP();
	}
}

//-----------------------------------------------------------------------------
// Initialize global data structure
//-----------------------------------------------------------------------------

void initGlobalData(void)
{
	uint8_t n;
	t_heater *heater;

	data.tempC = 0;
	data.relHum = 0;
	data.dewPointC = 0;
	data.sensorVersion = 0;
	data.tempAux = 0;
	data.voltage = 0;
	data.current = 0;
	data.power = 0;
	data.dpOffset = 3.0;
	data.skyTemp = -40;
	data.fudgeFactor = 1.0;

	for (n = 0; n < NUM_CHANNELS; n++) {
		heater = &(data.heater)[n];
		heater->lensDia = 4;
		heater->status = CH_UNCHECKED;
		heater->mode = MODE_AUTO;
		heater->Pmax = 0;
		heater->Pset = -1;
		heater->Preq = 0;
		heater->Patt = 0;
		heater->current = 0;
	}
}

//-----------------------------------------------------------------------------
// Initialization
//-----------------------------------------------------------------------------

void initialize(void)
{
	OSCFRQ = 0b00000010; // 4 MHz
	OSCCON1 = 0b01100000; // HINTOSC (1-32MHz), CDIV = 1
	while (!OSCCON3bits.ORDY); // Wait until clock switch is done

	// Peripheral Pin Select (PPS)
	RX1DTPPSbits.RX1DTPPS = 0x17; //RC7->EUSART1:RX1;
	RC6PPS = 0x0F; //RC4->EUSART1:TX1;    

	// Analog/digital IO
	ANSELA = 0b01000000; // RA6: aux. temp. sensor analog input
	ANSELB = 0b00000000; // PORTB is digital only
	ANSELC = 0b00000011; // RC0: VSENS, RC1: ISENS

	// Data direction registers
	TRISA = 0b11110000; // Outputs: RA0..3: SW_CH1..4, Inputs: RA4..7
	TRISB = 0b00000000;
	TRISC = 0b10000111; // Inputs: RC7: RX, RC2: nFAULT, RC1: ISENS, RC0: VSENS
	LATA = 0;

	// ADC
	ADCON0bits.ADON = 1;
	ADCON1 = 0b11100000; // Right justified, Fosc/64, Vref+=Vdd

	// Timer0: 10ms 
	T0CON0 = 0b10000000; // Enabled, 8-bit mode, postscaler 1:1
	T0CON1 = 0b01000111; // Clock Fosc/4, sync to Fosc, prescaler 1:128
	TMR0 = TMR0_PRELOAD;

	// Timer1: 100ms
	T1CON = 0b00110011; // Prescaler 1:8, 16-bit rd/wr, enabled
	T1CLK = 0b00000001; // Clock Fosc/4
	TMR1 = TMR1_PRELOAD;

	// Interrupts
	PIE0 = 0b00110000; // TMR0IE, IOCIE
	PIE3 = 0b00100000; // RC1IE
	PIE4 = 0b00000001; // TMR1IE
	INTCON = 0b11000000; // GIE, PEIE

	// Interrupt-on-change
	IOCAP = 0b10110000; // Pos. edge on RA7, RA5, RA4 (PB, ROT_B, ROT_A)
	IOCAN = 0b10110000; // Neg. edge on RA7, RA5, RA4
	IOCCN = 0b00000100; // Neg. edge on RC2 (nFAULT)

	// EUSART
	// SYNC = 0, BRGH = 0, BRG16 = 1, SPBRG = 25 -> 9615 Baud (0.16% error)
	BAUD1CON = 0b00001000; // BRG16 = 1
	SPBRGL = 25;
	RC1STA = 0b10010000; // SPEN = 1, CREN = 1
	TX1STA = 0b00100000; // TXEN = 1
}

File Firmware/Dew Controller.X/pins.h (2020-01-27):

/* 
 * File:   pins.h
 * Author: Andre
 *
 * Created on 12. Januar 2020, 17:44
 */

#ifndef PINS_H
#define	PINS_H

#define SW_CH0      LATAbits.LATA0
#define SW_CH1      LATAbits.LATA1
#define SW_CH2      LATAbits.LATA2
#define SW_CH3      LATAbits.LATA3

#define ROT_A       PORTAbits.RA4
#define ROT_B       PORTAbits.RA5
#define ROT_PB      PORTAbits.RA7

#define OLED_DB3    LATCbits.LATC4
#define OLED_DB2    LATCbits.LATC5
#define OLED_DB1    LATBbits.LATB0
#define OLED_DB0    LATBbits.LATB1
#define OLED_EN     LATBbits.LATB2
#define OLED_RW     LATBbits.LATB3
#define OLED_RS     LATBbits.LATB4
#define OLED_PWR   LATBbits.LATB5

#define OLED_DB3_IN PORTCbits.RC4
#define OLED_DB3_T  TRISCbits.TRISC4

#define PEN         LATCbits.LATC3
#define nFAULT      PORTCbits.RC2

#define AIN_VSENS   0b010000
#define AIN_ISENS   0b010001
#define AIN_TEMP    0b000110

#endif	/* PINS_H */

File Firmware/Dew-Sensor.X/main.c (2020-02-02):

/*
 * File:   main.c
 * Author: Andre
 *
 * Created on 12. Januar 2020, 13:20
 */

#define _XTAL_FREQ  4000000UL

#include <xc.h>
#include <stdio.h>
#include <stdlib.h>
#include <stdint.h>
#include <math.h>
#include "config.h"

//-----------------------------------------------------------------------------
// Definitions
//-----------------------------------------------------------------------------
#define B 17.67 // constants needed for dewpoint calculation
#define C 243.5

typedef struct {
	uint8_t header;
	uint8_t version;
	uint8_t status;
	float tempC;
	float relHum;
	float dewPointC;
} t_dataPacket;

typedef enum {
	NO_COMMAND,
	GET_DATA,
	UNKNOWN_COMMAND
} t_commands;

//-----------------------------------------------------------------------------
// Global Data
//-----------------------------------------------------------------------------

volatile uint8_t g_rxFErrCount = 0;
volatile uint8_t g_rxOErrCount = 0;
volatile t_commands g_command;

//-----------------------------------------------------------------------------
// Function Prototypes
//-----------------------------------------------------------------------------

void initialize(void);
void uartSendByte(char s);
void uartReceiveISR(void);
void i2cStart(void);
void i2cStop(void);
void i2cRepeat(void);
uint8_t i2cRead(uint8_t *readBuffer, uint8_t numBytes, uint8_t address);
uint8_t i2cWrite(uint8_t *writeBuffer, uint8_t numBytes, uint8_t address);
uint8_t readSI7006(float *RH, float *tempC, float *DP);

//-----------------------------------------------------------------------------
// Main program loop
//-----------------------------------------------------------------------------

void main(void)
{
	char *s;
	char checksum;
	t_dataPacket dataPacket;
	uint8_t n;

	initialize();

	while (1) {
		CLRWDT();
		switch (g_command) {
		case GET_DATA:
			dataPacket.header = 0xAA;
			dataPacket.version = 10;

			dataPacket.status = 0;
			if (readSI7006(&dataPacket.relHum, &dataPacket.tempC, &dataPacket.dewPointC)) {
				if ((dataPacket.tempC >= -50) && (dataPacket.tempC <= 100) &&
					(dataPacket.dewPointC >= -50) && (dataPacket.dewPointC <= 100) &&
					(dataPacket.relHum >= 0) && (dataPacket.relHum <= 100))
					dataPacket.status = 1;
			}

			s = (char *) &dataPacket;
			checksum = 0;
			for (n = 0; n < sizeof(t_dataPacket); n++) {
				checksum ^= *s;
				uartSendByte(*(s++));
			}
			uartSendByte(checksum);

			g_command = NO_COMMAND;
			break;
		case UNKNOWN_COMMAND:
			uartSendByte(0xFF);
			g_command = NO_COMMAND;
			break;
		default:
			break;
		}
	}
}

//-----------------------------------------------------------------------------
// Read humidity and temperature values from SI7006 sensor
//-----------------------------------------------------------------------------

uint8_t readSI7006(float *RH, float *tempC, float *DP)
{
	uint8_t buffer[2];
	float gamma;

	i2cStart();
	buffer[0] = 0xE5; // measure relative humidity, hold master mode
	if (!i2cWrite(buffer, 1, 0x40))
		return 0;
	i2cRepeat();
	if (!i2cRead(buffer, 2, 0x40))
		return 0;
	i2cStop();

	*RH = (125.0 * ((uint16_t) buffer[0] << 8 | (uint16_t) buffer[1]) / 65536) - 6;

	i2cStart();
	buffer[0] = 0xE0; // get temperature from last humidity measurement
	if (!i2cWrite(buffer, 1, 0x40))
		return 0;
	i2cRepeat();
	if (!i2cRead(buffer, 2, 0x40))
		return 0;
	i2cStop();

	*tempC = (175.72 * ((uint16_t) buffer[0] << 8 | (uint16_t) buffer[1]) / 65536) - 46.85;

	gamma = log(*RH / 100.0) + ((B * *tempC) / (C + *tempC));
	*DP = (C * gamma) / (B - gamma);

	return 1;
}

//-----------------------------------------------------------------------------
// Generate I2C start condition
//-----------------------------------------------------------------------------

void i2cStart(void)
{
	PIR3bits.SSP1IF = 0;
	SSP1CON2bits.SEN = 1;
	while (!PIR3bits.SSP1IF);
	PIR3bits.SSP1IF = 0;
}

//-----------------------------------------------------------------------------
// Generate I2C stop condition
//-----------------------------------------------------------------------------

void i2cStop(void)
{
	SSP1CON2bits.PEN = 1;
	while (!PIR3bits.SSP1IF);
	PIR3bits.SSP1IF = 0;
}

//-----------------------------------------------------------------------------
// Generate I2C repeat condition
//-----------------------------------------------------------------------------

void i2cRepeat(void)
{
	SSP1CON2bits.RSEN = 1;
	while (!PIR3bits.SSP1IF);
	PIR3bits.SSP1IF = 0;
}

//-----------------------------------------------------------------------------
// Writes numBytes from writeBuffer to I2C device
//-----------------------------------------------------------------------------

uint8_t i2cWrite(uint8_t *writeBuffer, uint8_t numBytes, uint8_t address)
{
	uint8_t n;

	SSP1BUF = address << 1;
	while (!PIR3bits.SSP1IF);
	PIR3bits.SSP1IF = 0;
	if (SSP1CON2bits.ACKSTAT)
		return 0;
	for (n = 0; n < numBytes; n++) {
		SSP1BUF = writeBuffer[n];
		while (!PIR3bits.SSP1IF);
		PIR3bits.SSP1IF = 0;
		if (SSP1CON2bits.ACKSTAT)
			return n;
	}
	return n;
}

//-----------------------------------------------------------------------------
// Read numBytes from I2C device into readBuffer
//-----------------------------------------------------------------------------

uint8_t i2cRead(uint8_t *readBuffer, uint8_t numBytes, uint8_t address)
{
	SSP1BUF = (address << 1) | 0x01;
	while (!PIR3bits.SSP1IF);
	PIR3bits.SSP1IF = 0;
	if (SSP1CON2bits.ACKSTAT)
		return 0;
	while (numBytes--) {
		SSP1CON2bits.RCEN = 1;
		while (!PIR3bits.SSP1IF);
		PIR3bits.SSP1IF = 0;
		*readBuffer++ = SSP1BUF;

		SSP1CON2bits.ACKDT = (numBytes ? 0 : 1);
		SSP1CON2bits.ACKEN = 1;
		while (!PIR3bits.SSP1IF);
		PIR3bits.SSP1IF = 0;
	}
	return 1;
}

//-----------------------------------------------------------------------------
// Transmit single byte over UART
//-----------------------------------------------------------------------------

void uartSendByte(char s)
{
	TX1REG = s;
	NOP();
	while (!PIR3bits.TX1IF);
}

//-----------------------------------------------------------------------------
// Initialization
//-----------------------------------------------------------------------------
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

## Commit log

2019-08-02 Merged repos
    [Calc.ods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]
2019-08-02 Added Case Design Files (Schaeffer AG)
2020-01-14 Rewriting firmware from scratch
    [Calc.ods]
2020-01-18 added I2C code for dew sensor
2020-01-18 Finished I2C code. Dew Sensor sends data packets.
2020-01-28 Replaced all sprintf() with ftoa(). Testing Pset/Pmax/Preq...
    [main.c, menu.c, menuhelper.c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]
2020-01-28 samples = 0
2020-01-29 Push button now checked on 10ms timer isr after first push.
2020-01-30 Added error handling and the channelThing(tm)
    [inputs.c, io.c, io.h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]
2020-02-01 Storing configuration in flash memory.
    [Berechnungen.xlsx, Calc.ods, Heizungen.xlsx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]
2020-02-02 Update sensor firmware. Clearing status bit when sensor data is implausible.
2020-02-03 strnycpy bug fixed and fortuitous compiler farts galore...
    [main.c, menuhelper.c, system.c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]
2020-02-13 Updated schematics
